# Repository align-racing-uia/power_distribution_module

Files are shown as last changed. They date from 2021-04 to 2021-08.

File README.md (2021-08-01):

<h1 align="center"> Power Distribution Module </h1> <br>
<p align="center">
    <a href="http://www.alignracing.no/">
      Align Racing UiA
    </a>
</p>

<!-- START doctoc generate TOC please keep comment here to allow auto update -->
<!-- DON'T EDIT THIS SECTION, INSTEAD RE-RUN doctoc TO UPDATE -->
## Table of contents

- [Introduction](#introduction)
- [Align Racing UiA](#alignracinguia)
- [Rules for file structure](#rulesforfilestructure)
- [License](#license)

<!-- END doctoc generated TOC please keep comment here to allow auto update -->

## Introduction

This is the repository for Align Racing's formula student race car's different systems.

## Align Racing UiA

<a href="http://www.alignracing.no/">Align Racing UiA (AR)</a> is a multidisciplinary student organisation at <a href="https://www.uia.no/">The University of Agder (UiA)</a>, that take part in the world’s largest yearly engineering competition; <a href="https://www.imeche.org/events/formula-student">Formula Student (FS)</a>. The organisation continuously consists of around 60 students, from a wide variety of disciplines. The competition includes developing, building, budgeting and marketing a small scale formula type racing car. AR takes this a bit further by having more focus on developing a strong organisation, open for all disciplines, that gives the members a taste of future work-life.

## Rules

## Contribution

## License
All content included in this Git repository is under the license:

Creative Commons Attribution-NonCommercial-ShareAlike 4.0 International

You are free to:
* <b> Share </b> — copy and redistribute the material in any medium or format
* <b> Adapt </b> — remix, transform, and build upon the material

Under the following terms:
* <b> Attribution </b> — You must give appropriate credit, provide a link to the license, and indicate if changes were made. You may do so in any reasonable manner, but not in any way that suggests the licensor endorses you or your use.
* <b> NonCommercial </b> — You may not use the material for commercial purposes.
* <b> ShareAlike </b> — If you remix, transform, or build upon the material, you must distribute your contributions under the same license as the original.
* <b> No additional restrictions </b> — You may not apply legal terms or technological measures that legally restrict others from doing anything the license permits.

<p align="center">
License
</p>

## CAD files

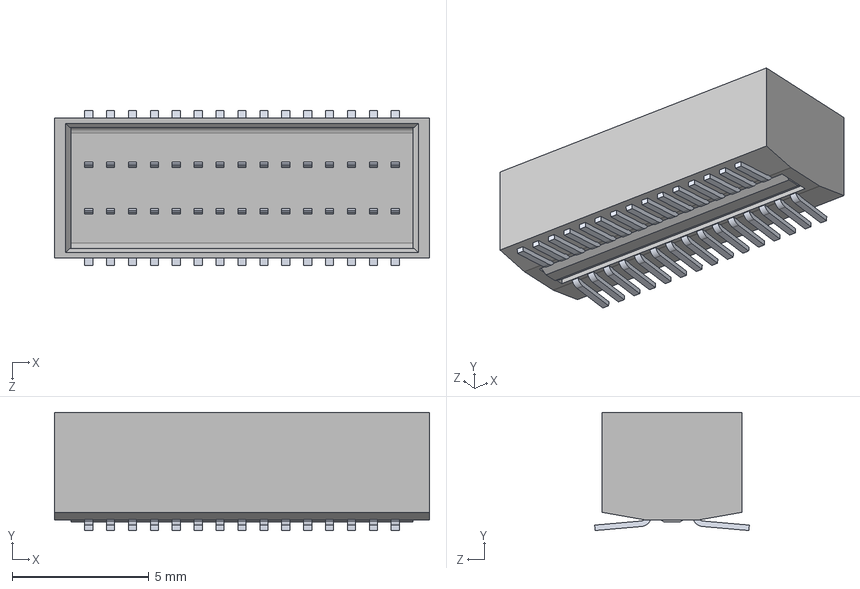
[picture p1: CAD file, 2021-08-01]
pdm_pcb/AR_PDM_v1/3d_objects/ACM-connector-pcb.step
13.7 x 4.31 x 5.65 mm

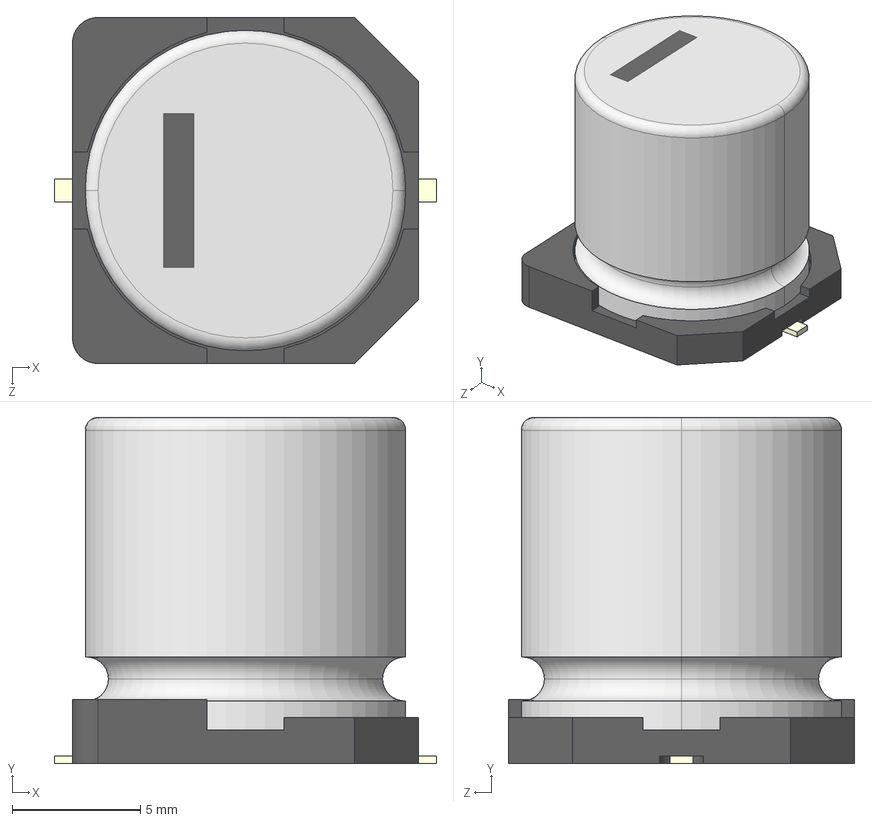
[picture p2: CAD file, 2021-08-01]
pdm_pcb/AR_PDM_v1_Simplified/3d_objects/H13.STEP
14.9 x 13.5 x 13.5 mm
標準SIZE CODE H13-001
標準SIZE CODE H13-002
標準SIZE CODE H13-003 x 2

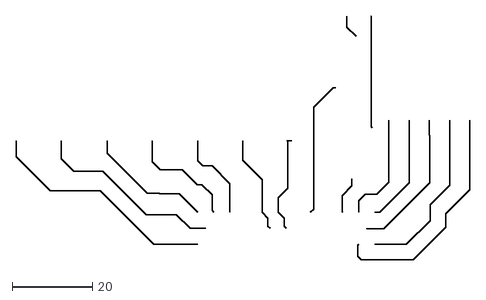
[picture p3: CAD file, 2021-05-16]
pdm_pcb/AR_PDM_v1_Simplified/test export/AR20_PDM_v1-F_Cu.dxf
112.8 x 60.5

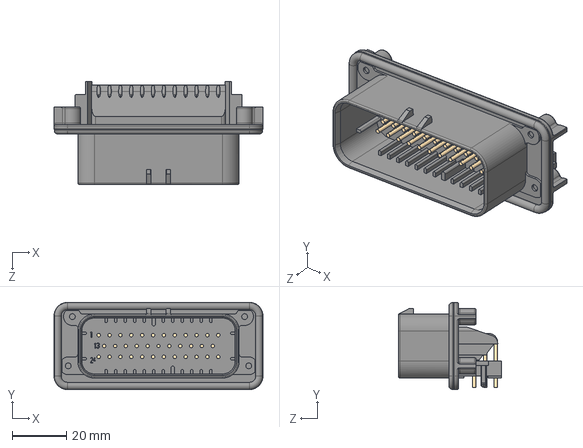
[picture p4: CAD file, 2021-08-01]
pdm_pcb/AR_PDM_v1/3d_objects/c-1-776163-1-s-3d.STEP
76.9 x 32.1 x 37.8 mm

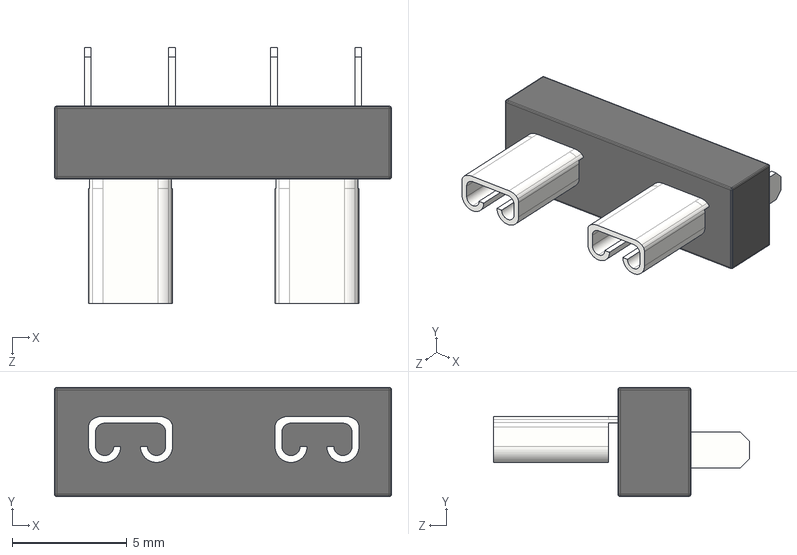
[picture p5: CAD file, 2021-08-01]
pdm_pcb/AR_PDM_v1_Simplified/3d_objects/Mini Blade Fuse Holder.STEP
14.7 x 4.75 x 11.1 mm
Body.step
Pins.step

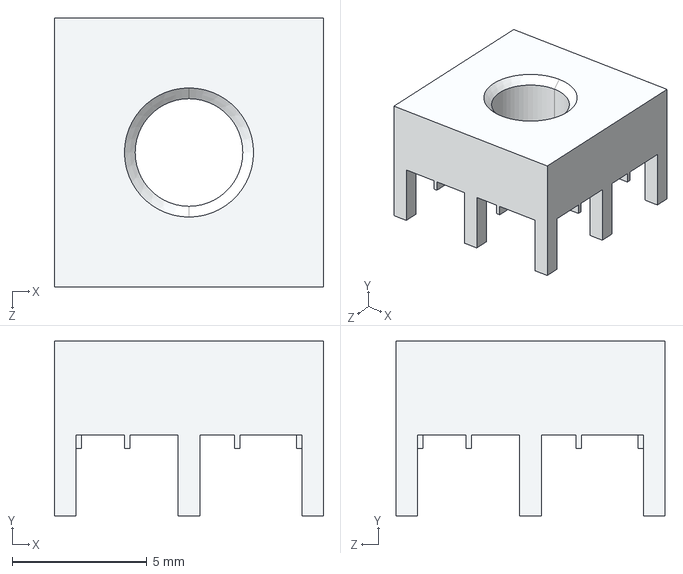
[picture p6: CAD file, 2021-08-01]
pdm_pcb/AR_PDM_v1/3d_objects/Wurth Studd m5.STEP
10.0 x 6.50 x 10.0 mm

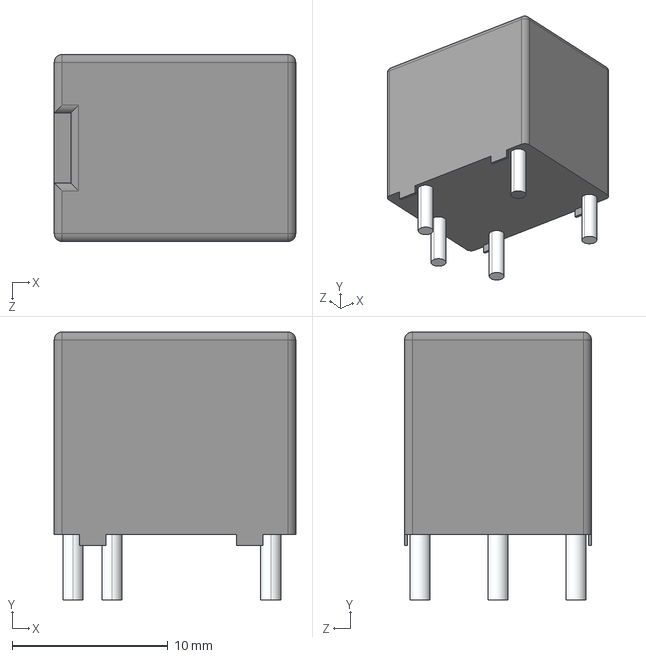
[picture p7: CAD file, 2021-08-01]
pdm_pcb/AR_PDM_v1/3d_objects/Relay.STEP
15.5 x 17.2 x 12.0 mm

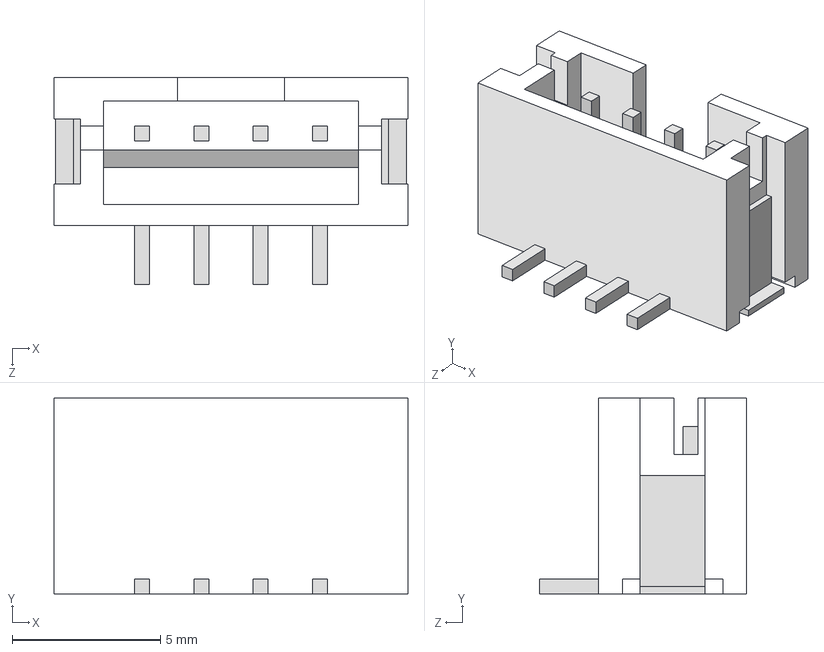
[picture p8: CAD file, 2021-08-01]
pdm_pcb/AR_PDM_v1_Simplified/3d_objects/B4B-PH-SM4-TB.STEP
12.0 x 6.60 x 7.00 mm

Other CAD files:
pdm_pcb/AR_PDM_v1_Simplified/3d_objects/Panasonic FK H13.STEP
pdm_pcb/AR_PDM_v1/3d_objects/Panasonic FK H13.STEP

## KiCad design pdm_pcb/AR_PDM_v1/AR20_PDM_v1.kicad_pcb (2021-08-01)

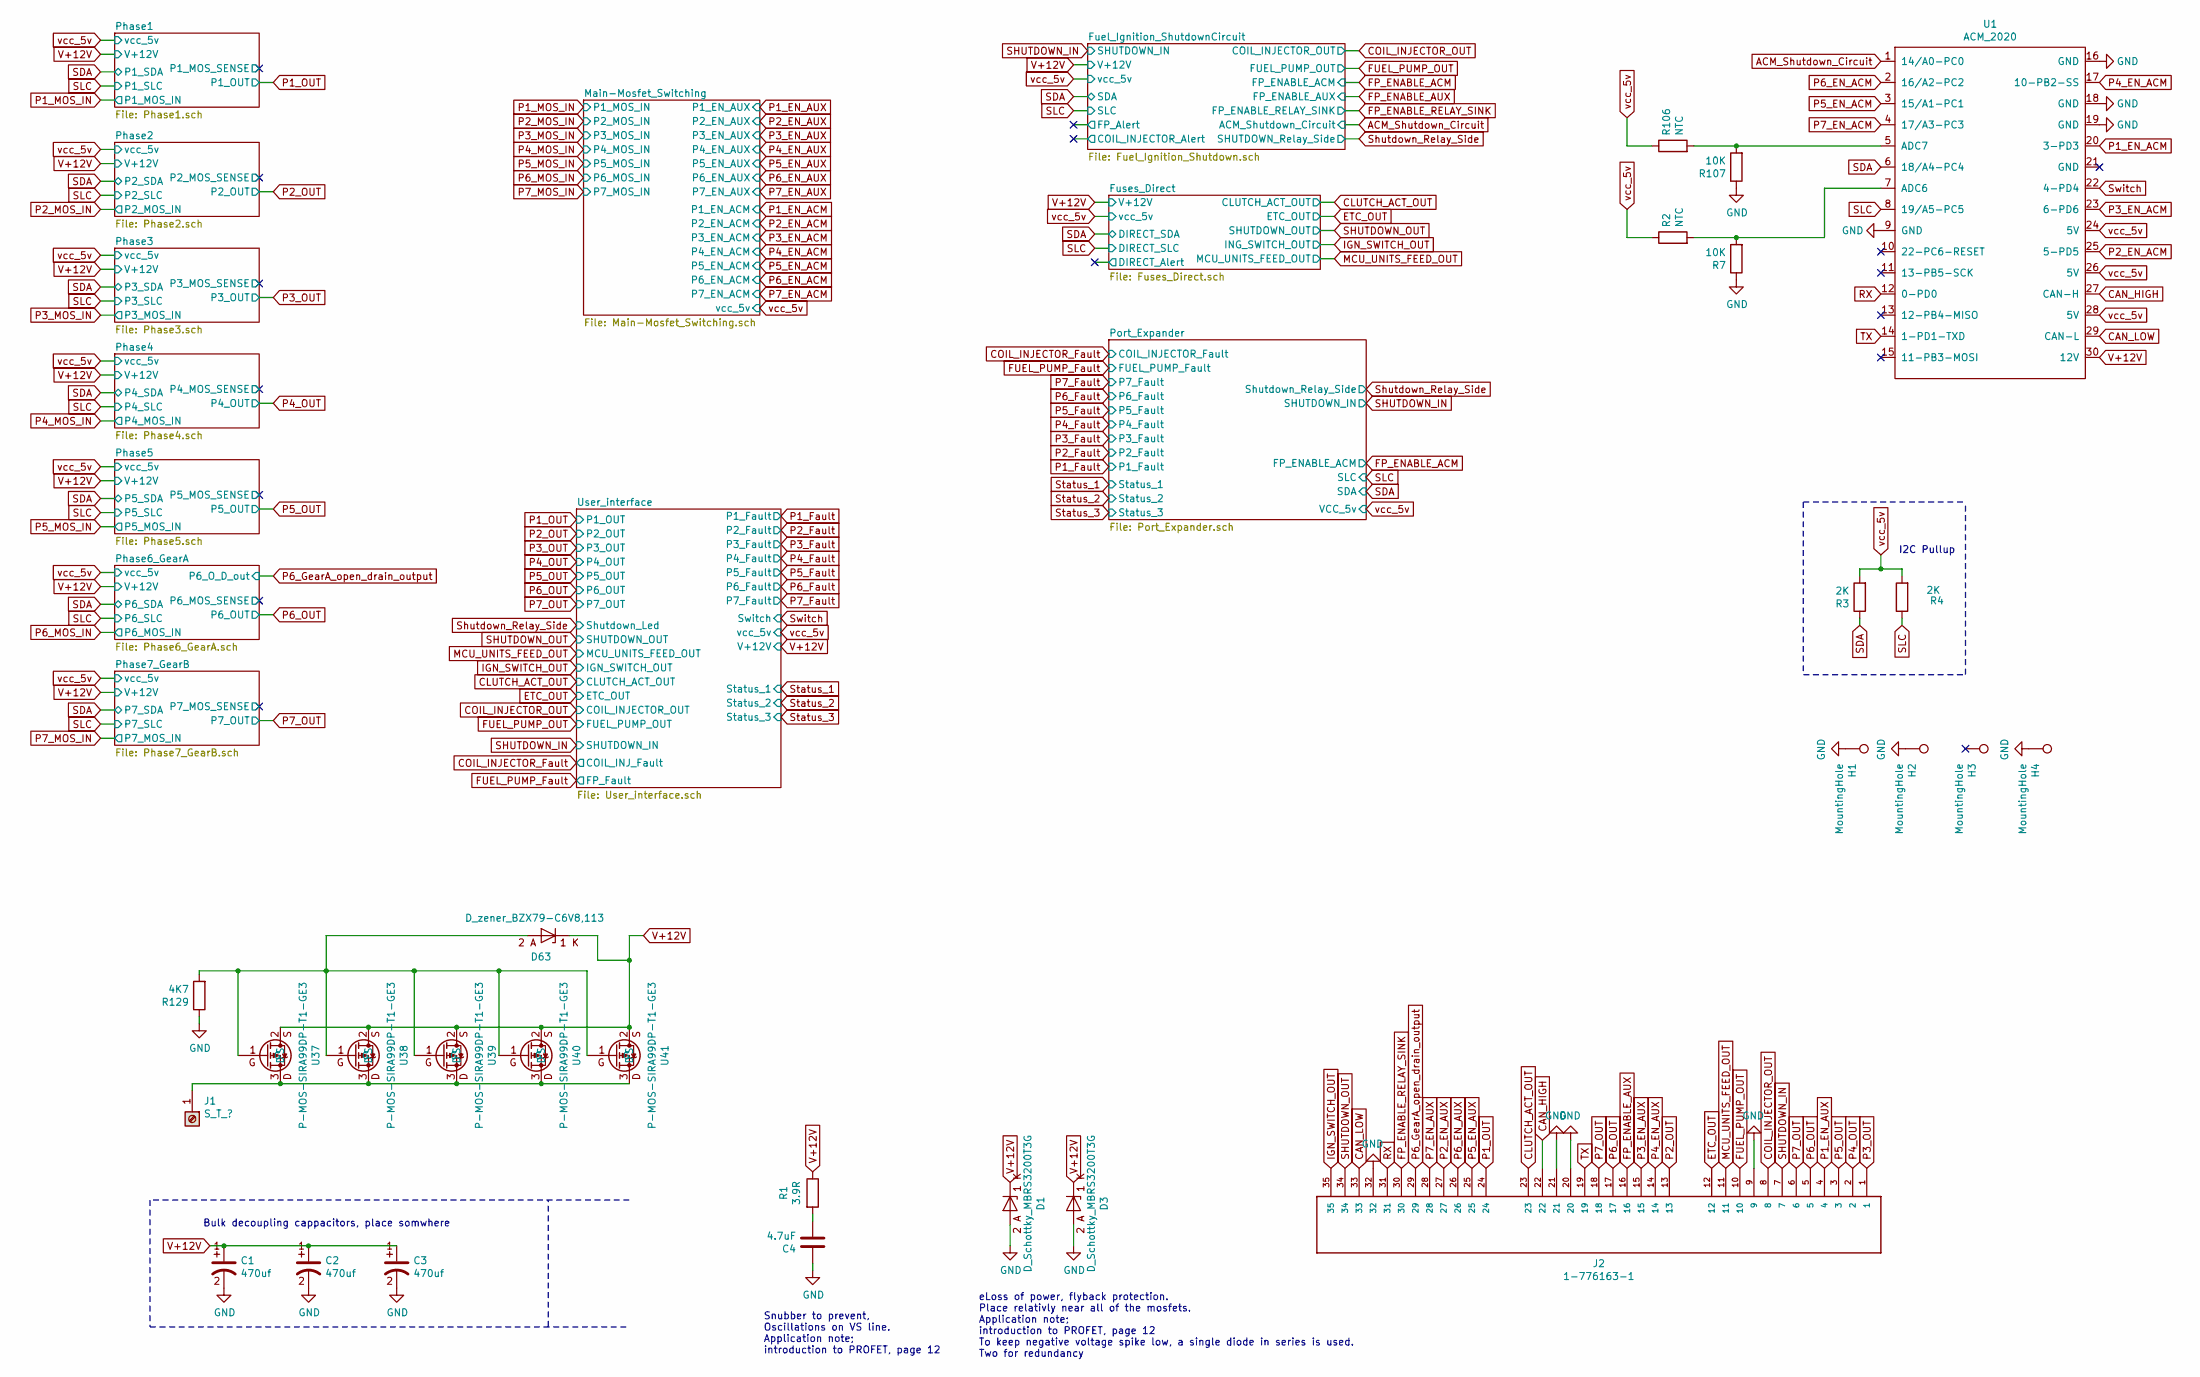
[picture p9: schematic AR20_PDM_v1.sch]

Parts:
C1, C2, C3: 470uf; CAPAE1350X1400N_EEV-FK1V471Q
C4: 4.7uF; C_1206_3216Metric
D1, D3: D_Schottky_MBRS3200T3G; D_SMB_Handsoldering
D63: D_zener_BZX79-C6V8,113; D_DO-35_BZX79-C6V8,113
H1, H2, H3, H4: MountingHole; MountingHole_3.2mm_M3_Pad_Via
J1: S_T_?; Wurth_74655095R_Screw_Post
J2: 1-776163-1; TE_1-776163-1
R1: 3.9R; R_2512_6332Metric
R2, R106: NTC; R_0603_1608Metric
R3, R4: 2K; R_0603_1608Metric
R7, R107: 10K; R_0603_1608Metric
R129: 4K7; R_0603_1608Metric
U1: ACM_2020; ACM_2020_Footprint_wo_silk
U37, U38, U39, U40, U41: P-MOS-SIRA99DP-T1-GE3

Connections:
ACM_Shutdown_Circuit: U1.1 (14/A0-PC0); also elsewhere on the board
CAN_HIGH: J2.22, U1.27 (CAN-H)
CAN_LOW: J2.33, U1.29 (CAN-L)
CLUTCH_ACT_OUT: J2.23; also elsewhere on the board
COIL_INJECTOR_OUT: J2.8; also elsewhere on the board
ETC_OUT: J2.12; also elsewhere on the board
FP_ENABLE_AUX: J2.16; also elsewhere on the board
FP_ENABLE_RELAY_SINK: J2.30; also elsewhere on the board
FUEL_PUMP_OUT: J2.10; also elsewhere on the board
IGN_SWITCH_OUT: J2.35; also elsewhere on the board
MCU_UNITS_FEED_OUT: J2.11; also elsewhere on the board
unnamed: C4.2, R1.2
unnamed: D63.2 (A), R129.2, U37.1 (G), U38.1 (G), U39.1 (G), U40.1 (G), U41.1 (G)
unnamed: J1.1, U37.3 (D), U38.3 (D), U39.3 (D), U40.3 (D), U41.3 (D)
unnamed: R2.2, R7.2, U1.7 (ADC6)
unnamed: R106.2, R107.2, U1.5 (ADC7)
P1_EN_ACM: U1.20 (3-PD3); also elsewhere on the board
P1_EN_AUX: J2.4; also elsewhere on the board
P1_OUT: J2.24; also elsewhere on the board
P2_EN_ACM: U1.25 (5-PD5); also elsewhere on the board
P2_EN_AUX: J2.27; also elsewhere on the board
P2_OUT: J2.13; also elsewhere on the board
P3_EN_ACM: U1.23 (6-PD6); also elsewhere on the board
P3_EN_AUX: J2.15; also elsewhere on the board
P3_OUT: J2.1; also elsewhere on the board
P4_EN_ACM: U1.17 (10-PB2-SS); also elsewhere on the board
P4_EN_AUX: J2.14; also elsewhere on the board
P4_OUT: J2.2; also elsewhere on the board
P5_EN_ACM: U1.3 (15/A1-PC1); also elsewhere on the board
P5_EN_AUX: J2.25; also elsewhere on the board
P5_OUT: J2.3; also elsewhere on the board
P6_EN_ACM: U1.2 (16/A2-PC2); also elsewhere on the board
P6_EN_AUX: J2.26; also elsewhere on the board
P6_GearA_open_drain_output: J2.29; also elsewhere on the board
P6_OUT: J2.5, J2.17; also elsewhere on the board
P7_EN_ACM: U1.4 (17/A3-PC3); also elsewhere on the board
P7_EN_AUX: J2.28; also elsewhere on the board
P7_OUT: J2.6, J2.18; also elsewhere on the board
RX: J2.31, U1.12 (0-PD0)
SDA: R3.1, U1.6 (18/A4-PC4); also elsewhere on the board
SHUTDOWN_IN: J2.7; also elsewhere on the board
SHUTDOWN_OUT: J2.34; also elsewhere on the board
SLC: R4.1, U1.8 (19/A5-PC5); also elsewhere on the board
Switch: U1.22 (4-PD4); also elsewhere on the board
TX: J2.19, U1.14 (1-PD1-TXD)
V+12V: C1.1, C2.1, C3.1, D1.1 (K), D3.1 (K), D63.1 (K), R1.1, U1.30 (12V), U37.2 (S), U38.2 (S), U39.2 (S), U40.2 (S), U41.2 (S); also elsewhere on the board
vcc_5v: R2.1, R3.2, R4.2, R106.1, U1.24 (5V), U1.26 (5V), U1.28 (5V); also elsewhere on the board

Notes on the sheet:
Bulk decoupling cappacitors, place somwhere
eLoss of power, flyback protection. Place relativly near all of the mosfets. Application note; introduction to PROFET, page 12 To keep negative voltage spike low, a single diode in series is used. Two for redundancy
I2C Pullup
Snubber to prevent, Oscillations on VS line. Application note; introduction to PROFET, page 12

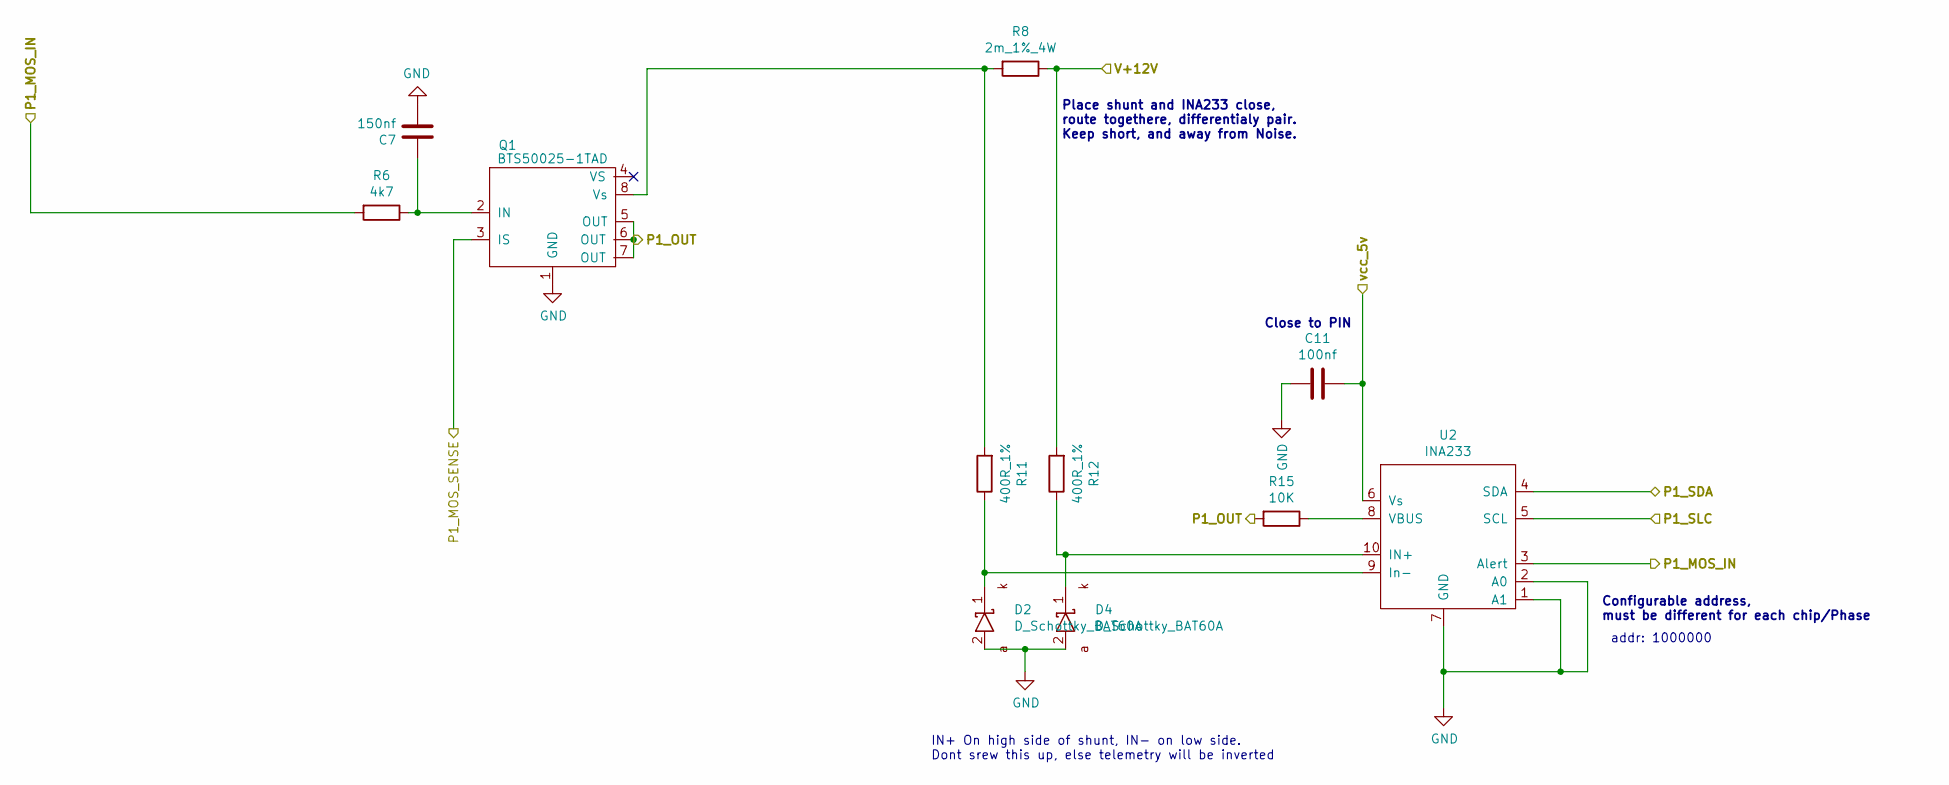
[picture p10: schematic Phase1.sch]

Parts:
C7: 150nf; C_0603_1608Metric
C11: 100nf; C_0603_1608Metric
D2, D4: D_Schottky_BAT60A; D_Shotky_BAT60_HandSoldering
Q1: BTS50025-1TAD; BTS500xx
R6: 4k7; R_0603_1608Metric
R8: 2m_1%_4W; R_2512_6332Metric
R11, R12: 400R_1%; R_0603_1608Metric
R15: 10K; R_0603_1608Metric
U2: INA233

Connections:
/Phase1/P1_MOS_SENSE: Q1.3 (IS)
unnamed: C7.1, Q1.2 (IN), R6.1
unnamed: D2.1 (K), R11.1, U2.9 (In-)
unnamed: D4.1 (K), R12.1, U2.10 (IN+)
unnamed: Q1.8 (Vs), R8.2, R11.2
unnamed: R15.1, U2.8 (VBUS)
P1_MOS_IN: R6.2, U2.3 (Alert); also elsewhere on the board
P1_OUT: Q1.5 (OUT), Q1.6 (OUT), Q1.7 (OUT), R15.2; also elsewhere on the board
SDA: U2.4 (SDA); also elsewhere on the board
SLC: U2.5 (SCL); also elsewhere on the board
V+12V: R8.1, R12.2; also elsewhere on the board
vcc_5v: C11.1, U2.6 (Vs); also elsewhere on the board

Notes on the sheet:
Close to PIN
Configurable address, must be different for each chip/Phase
addr: 1000000
Place shunt and INA233 close, route togethere, differentialy pair. Keep short, and away from Noise.
IN+ On high side of shunt, IN- on low side. Dont srew this up, else telemetry will be inverted

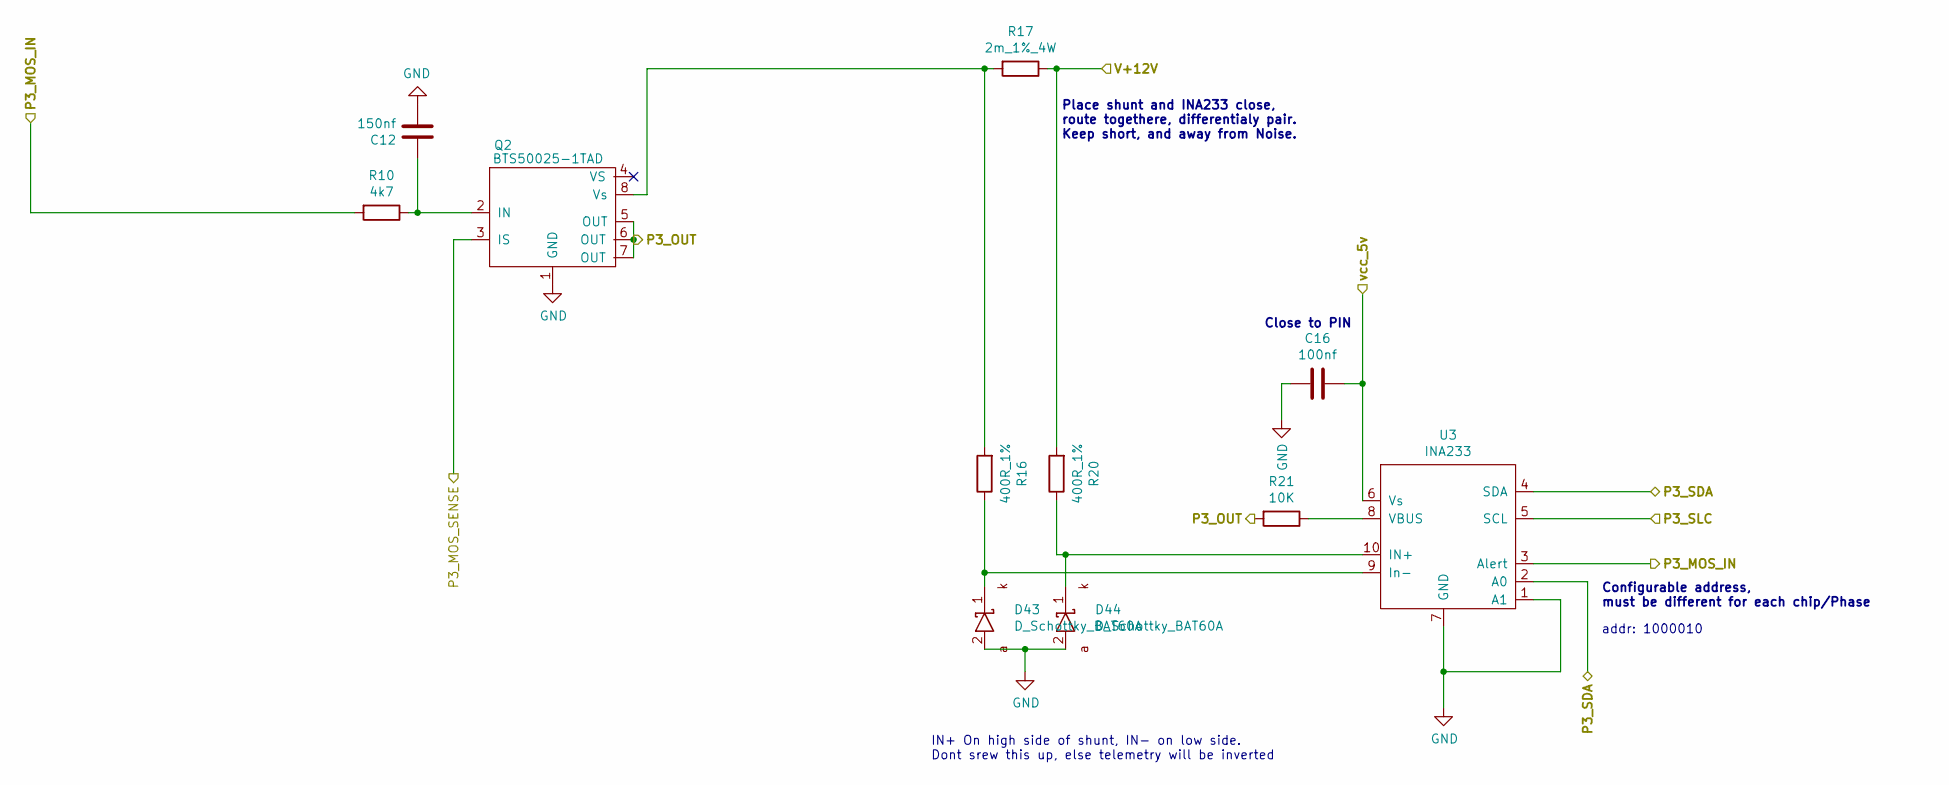
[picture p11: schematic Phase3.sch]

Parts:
C12: 150nf; C_0603_1608Metric
C16: 100nf; C_0603_1608Metric
D43, D44: D_Schottky_BAT60A; D_Shotky_BAT60_HandSoldering
Q2: BTS50025-1TAD; BTS500xx
R10: 4k7; R_0603_1608Metric
R16, R20: 400R_1%; R_0603_1608Metric
R17: 2m_1%_4W; R_2512_6332Metric
R21: 10K; R_0603_1608Metric
U3: INA233

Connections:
/Phase3/P3_MOS_SENSE: Q2.3 (IS)
unnamed: C12.1, Q2.2 (IN), R10.1
unnamed: D43.1 (K), R16.1, U3.9 (In-)
unnamed: D44.1 (K), R20.1, U3.10 (IN+)
unnamed: Q2.8 (Vs), R16.2, R17.2
unnamed: R21.1, U3.8 (VBUS)
P3_MOS_IN: R10.2, U3.3 (Alert); also elsewhere on the board
P3_OUT: Q2.5 (OUT), Q2.6 (OUT), Q2.7 (OUT), R21.2; also elsewhere on the board
SDA: U3.2 (A0), U3.4 (SDA); also elsewhere on the board
SLC: U3.5 (SCL); also elsewhere on the board
V+12V: R17.1, R20.2; also elsewhere on the board
vcc_5v: C16.1, U3.6 (Vs); also elsewhere on the board

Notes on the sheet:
Close to PIN
Configurable address, must be different for each chip/Phase
addr: 1000010
Place shunt and INA233 close, route togethere, differentialy pair. Keep short, and away from Noise.
IN+ On high side of shunt, IN- on low side. Dont srew this up, else telemetry will be inverted

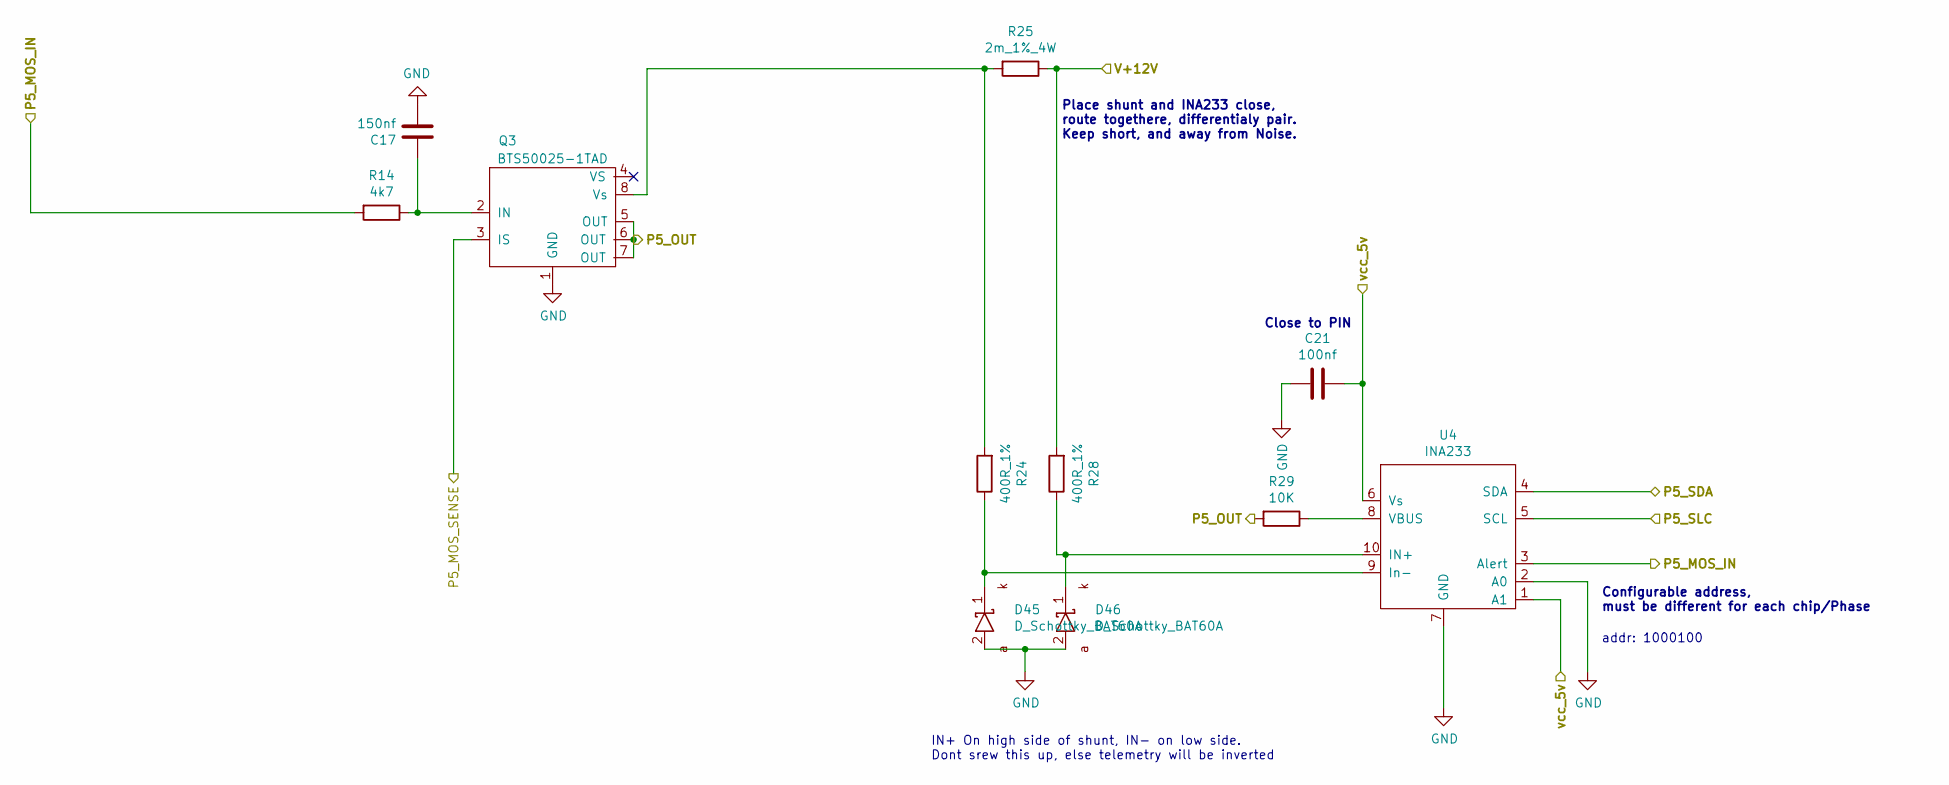
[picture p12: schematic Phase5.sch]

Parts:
C17: 150nf; C_0603_1608Metric
C21: 100nf; C_0603_1608Metric
D45, D46: D_Schottky_BAT60A; D_Shotky_BAT60_HandSoldering
Q3: BTS50025-1TAD; BTS500xx
R14: 4k7; R_0603_1608Metric
R24, R28: 400R_1%; R_0603_1608Metric
R25: 2m_1%_4W; R_2512_6332Metric
R29: 10K; R_0603_1608Metric
U4: INA233

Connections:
/Phase5/P5_MOS_SENSE: Q3.3 (IS)
unnamed: C17.1, Q3.2 (IN), R14.1
unnamed: D45.1 (K), R24.1, U4.9 (In-)
unnamed: D46.1 (K), R28.1, U4.10 (IN+)
unnamed: Q3.8 (Vs), R24.2, R25.2
unnamed: R29.1, U4.8 (VBUS)
P5_MOS_IN: R14.2, U4.3 (Alert); also elsewhere on the board
P5_OUT: Q3.5 (OUT), Q3.6 (OUT), Q3.7 (OUT), R29.2; also elsewhere on the board
SDA: U4.4 (SDA); also elsewhere on the board
SLC: U4.5 (SCL); also elsewhere on the board
V+12V: R25.1, R28.2; also elsewhere on the board
vcc_5v: C21.1, U4.1 (A1), U4.6 (Vs); also elsewhere on the board

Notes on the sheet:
Close to PIN
Configurable address, must be different for each chip/Phase
addr: 1000100
Place shunt and INA233 close, route togethere, differentialy pair. Keep short, and away from Noise.
IN+ On high side of shunt, IN- on low side. Dont srew this up, else telemetry will be inverted

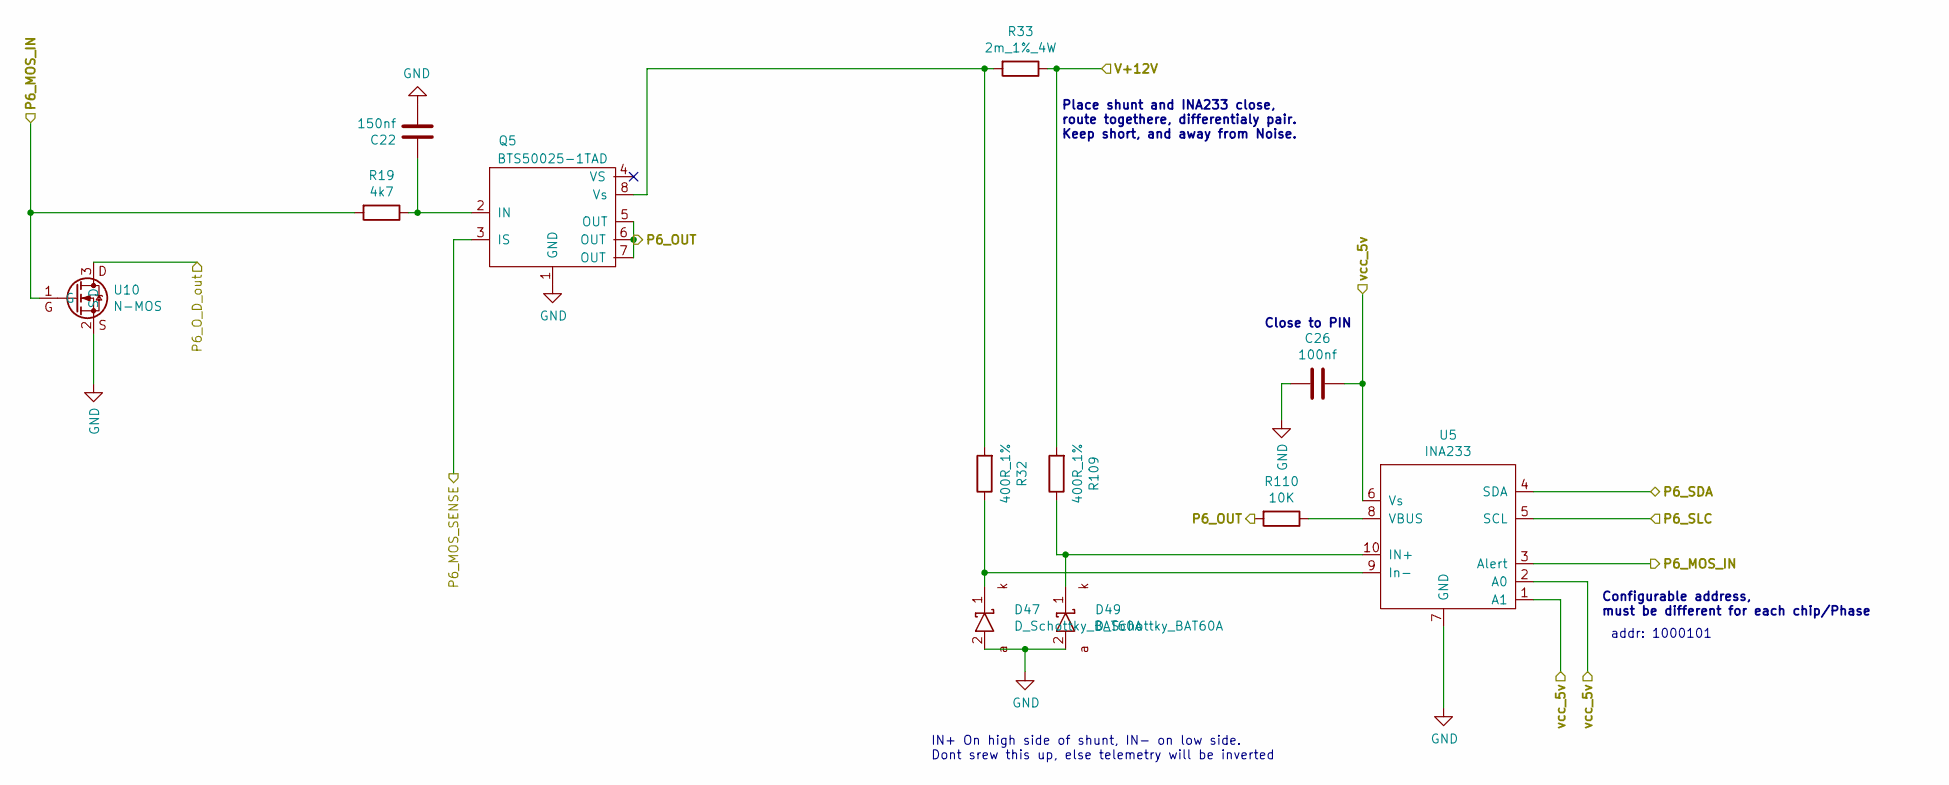
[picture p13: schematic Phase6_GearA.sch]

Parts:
C22: 150nf; C_0603_1608Metric
C26: 100nf; C_0603_1608Metric
D47, D49: D_Schottky_BAT60A; D_Shotky_BAT60_HandSoldering
Q5: BTS50025-1TAD; BTS500xx
R19: 4k7; R_0603_1608Metric
R32, R109: 400R_1%; R_0603_1608Metric
R33: 2m_1%_4W; R_2512_6332Metric
R110: 10K; R_0603_1608Metric
U5: INA233
U10: N-MOS; N-MOS-DMN6140L-13

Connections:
/Phase6_GearA/P6_MOS_SENSE: Q5.3 (IS)
unnamed: C22.1, Q5.2 (IN), R19.1
unnamed: D47.1 (K), R32.1, U5.9 (In-)
unnamed: D49.1 (K), R109.1, U5.10 (IN+)
unnamed: Q5.8 (Vs), R32.2, R33.2
unnamed: R110.1, U5.8 (VBUS)
P6_GearA_open_drain_output: U10.3 (D); also elsewhere on the board
P6_MOS_IN: R19.2, U5.3 (Alert), U10.1 (G); also elsewhere on the board
P6_OUT: Q5.5 (OUT), Q5.6 (OUT), Q5.7 (OUT), R110.2; also elsewhere on the board
SDA: U5.4 (SDA); also elsewhere on the board
SLC: U5.5 (SCL); also elsewhere on the board
V+12V: R33.1, R109.2; also elsewhere on the board
vcc_5v: C26.1, U5.1 (A1), U5.2 (A0), U5.6 (Vs); also elsewhere on the board

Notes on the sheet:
Close to PIN
Configurable address, must be different for each chip/Phase
addr: 1000101
Place shunt and INA233 close, route togethere, differentialy pair. Keep short, and away from Noise.
IN+ On high side of shunt, IN- on low side. Dont srew this up, else telemetry will be inverted

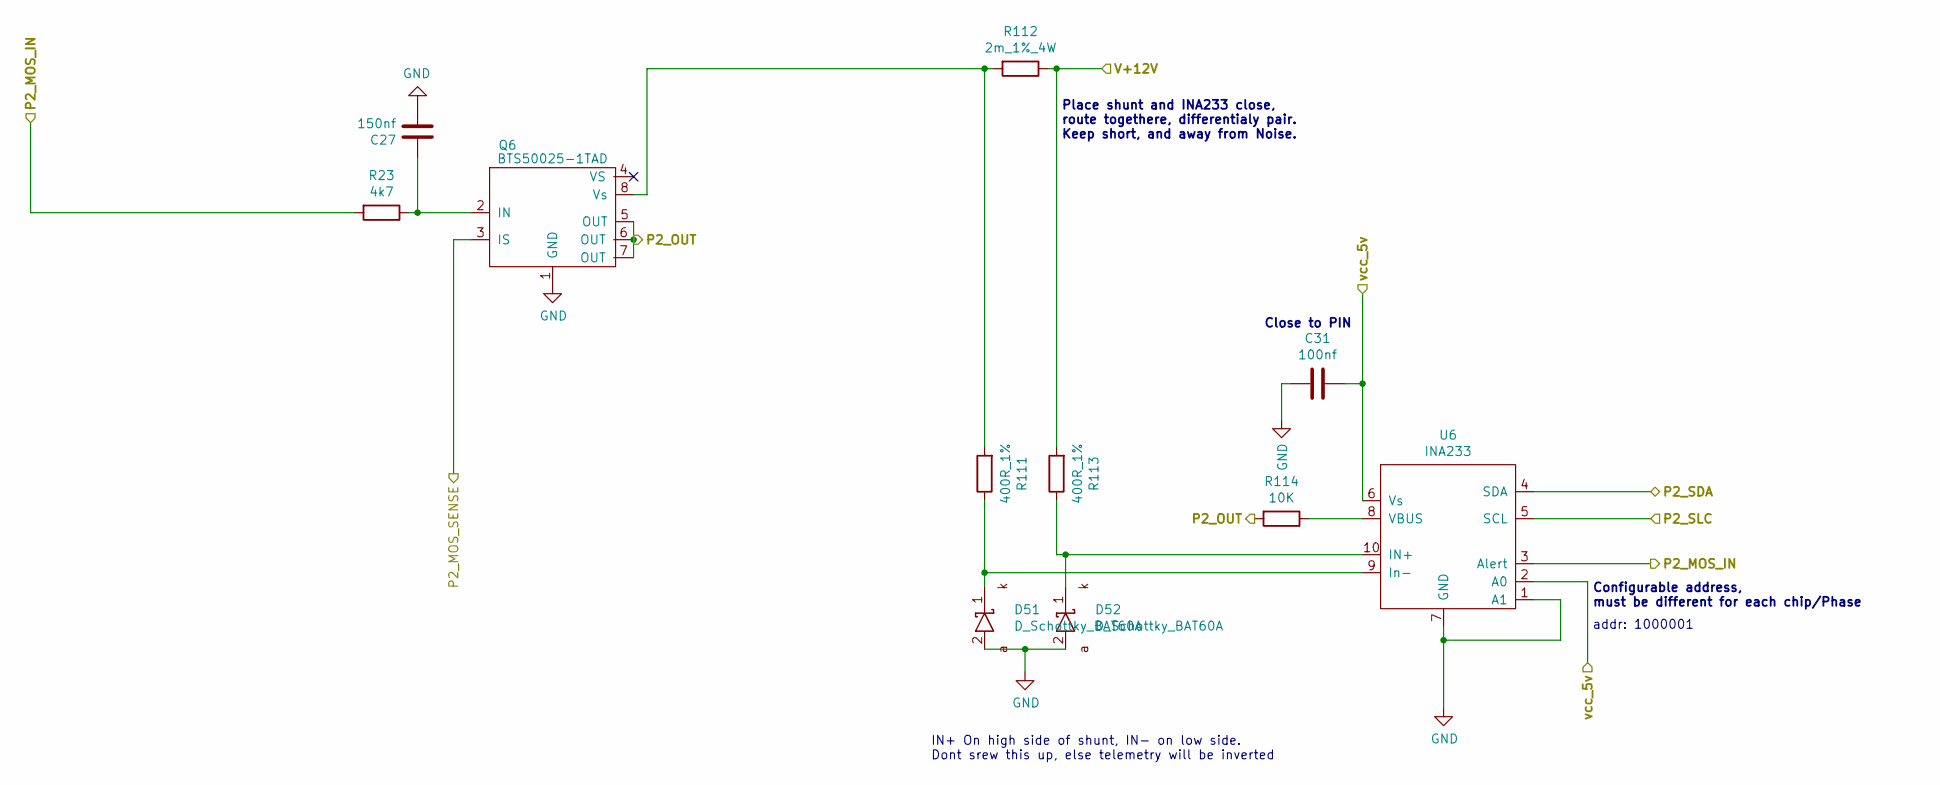
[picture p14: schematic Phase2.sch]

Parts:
C27: 150nf; C_0603_1608Metric
C31: 100nf; C_0603_1608Metric
D51, D52: D_Schottky_BAT60A; D_Shotky_BAT60_HandSoldering
Q6: BTS50025-1TAD; BTS500xx
R23: 4k7; R_0603_1608Metric
R111, R113: 400R_1%; R_0603_1608Metric
R112: 2m_1%_4W; R_2512_6332Metric
R114: 10K; R_0603_1608Metric
U6: INA233

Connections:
/Phase2/P2_MOS_SENSE: Q6.3 (IS)
unnamed: C27.1, Q6.2 (IN), R23.1
unnamed: D51.1 (K), R111.1, U6.9 (In-)
unnamed: D52.1 (K), R113.1, U6.10 (IN+)
unnamed: Q6.8 (Vs), R111.2, R112.2
unnamed: R114.1, U6.8 (VBUS)
P2_MOS_IN: R23.2, U6.3 (Alert); also elsewhere on the board
P2_OUT: Q6.5 (OUT), Q6.6 (OUT), Q6.7 (OUT), R114.2; also elsewhere on the board
SDA: U6.4 (SDA); also elsewhere on the board
SLC: U6.5 (SCL); also elsewhere on the board
V+12V: R112.1, R113.2; also elsewhere on the board
vcc_5v: C31.1, U6.2 (A0), U6.6 (Vs); also elsewhere on the board

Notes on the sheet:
Close to PIN
Configurable address, must be different for each chip/Phase
addr: 1000001
Place shunt and INA233 close, route togethere, differentialy pair. Keep short, and away from Noise.
IN+ On high side of shunt, IN- on low side. Dont srew this up, else telemetry will be inverted

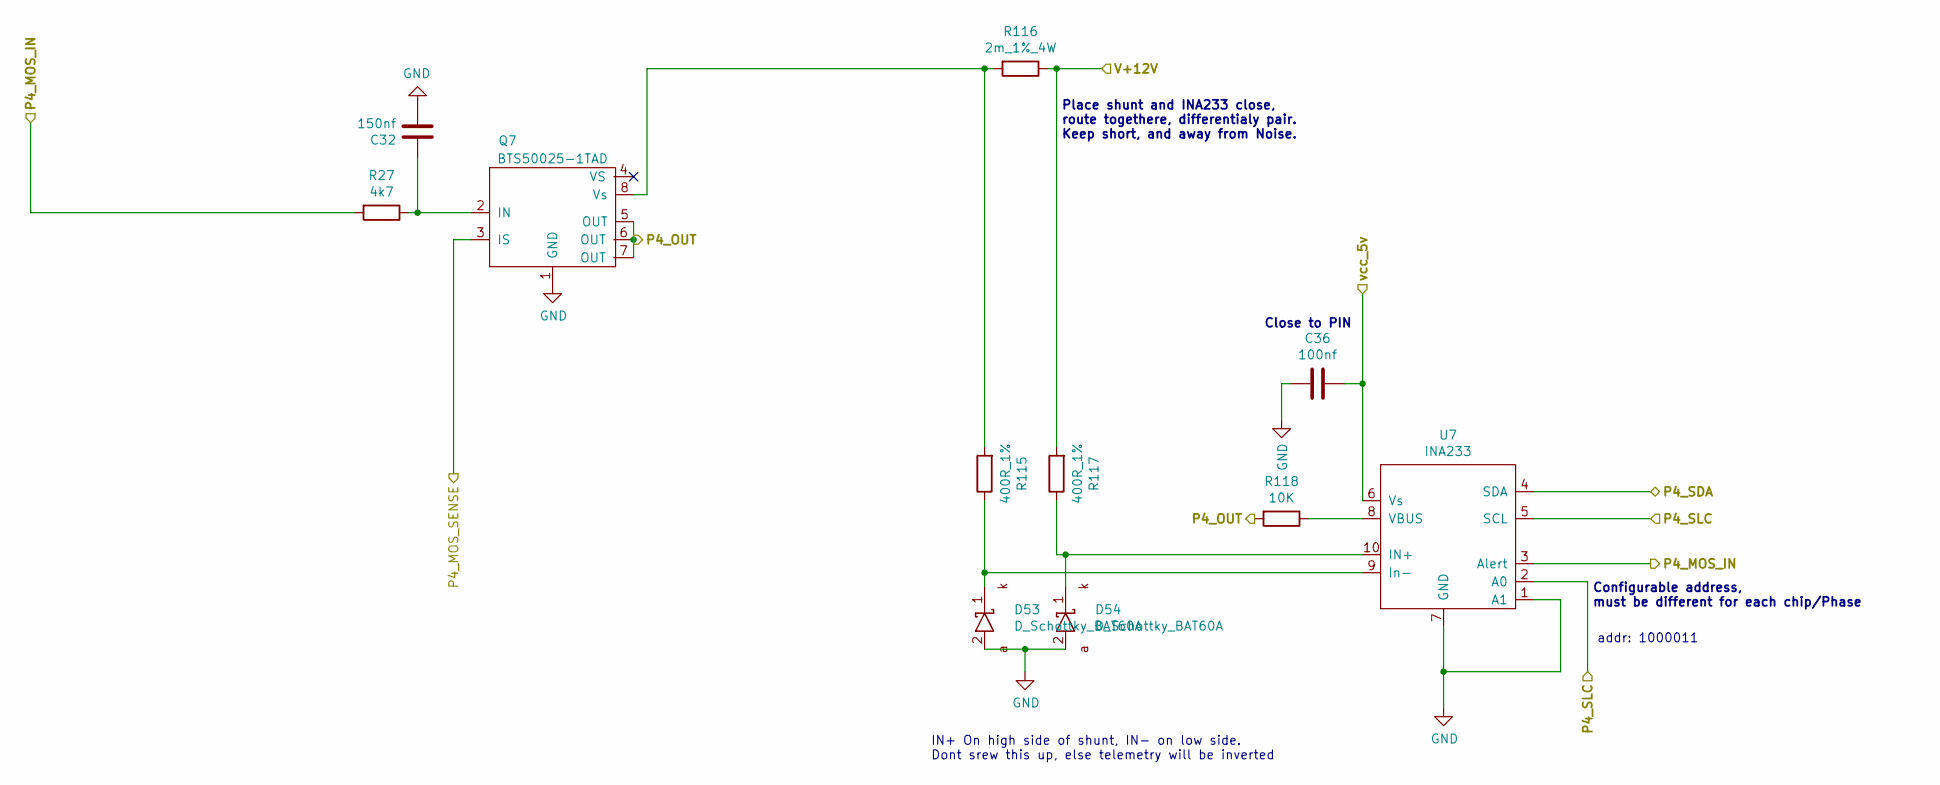
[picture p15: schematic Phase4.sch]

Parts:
C32: 150nf; C_0603_1608Metric
C36: 100nf; C_0603_1608Metric
D53, D54: D_Schottky_BAT60A; D_Shotky_BAT60_HandSoldering
Q7: BTS50025-1TAD; BTS500xx
R27: 4k7; R_0603_1608Metric
R115, R117: 400R_1%; R_0603_1608Metric
R116: 2m_1%_4W; R_2512_6332Metric
R118: 10K; R_0603_1608Metric
U7: INA233

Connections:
/Phase4/P4_MOS_SENSE: Q7.3 (IS)
unnamed: C32.1, Q7.2 (IN), R27.1
unnamed: D53.1 (K), R115.1, U7.9 (In-)
unnamed: D54.1 (K), R117.1, U7.10 (IN+)
unnamed: Q7.8 (Vs), R115.2, R116.2
unnamed: R118.1, U7.8 (VBUS)
P4_MOS_IN: R27.2, U7.3 (Alert); also elsewhere on the board
P4_OUT: Q7.5 (OUT), Q7.6 (OUT), Q7.7 (OUT), R118.2; also elsewhere on the board
SDA: U7.4 (SDA); also elsewhere on the board
SLC: U7.2 (A0), U7.5 (SCL); also elsewhere on the board
V+12V: R116.1, R117.2; also elsewhere on the board
vcc_5v: C36.1, U7.6 (Vs); also elsewhere on the board

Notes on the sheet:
Close to PIN
Configurable address, must be different for each chip/Phase
addr: 1000011
Place shunt and INA233 close, route togethere, differentialy pair. Keep short, and away from Noise.
IN+ On high side of shunt, IN- on low side. Dont srew this up, else telemetry will be inverted

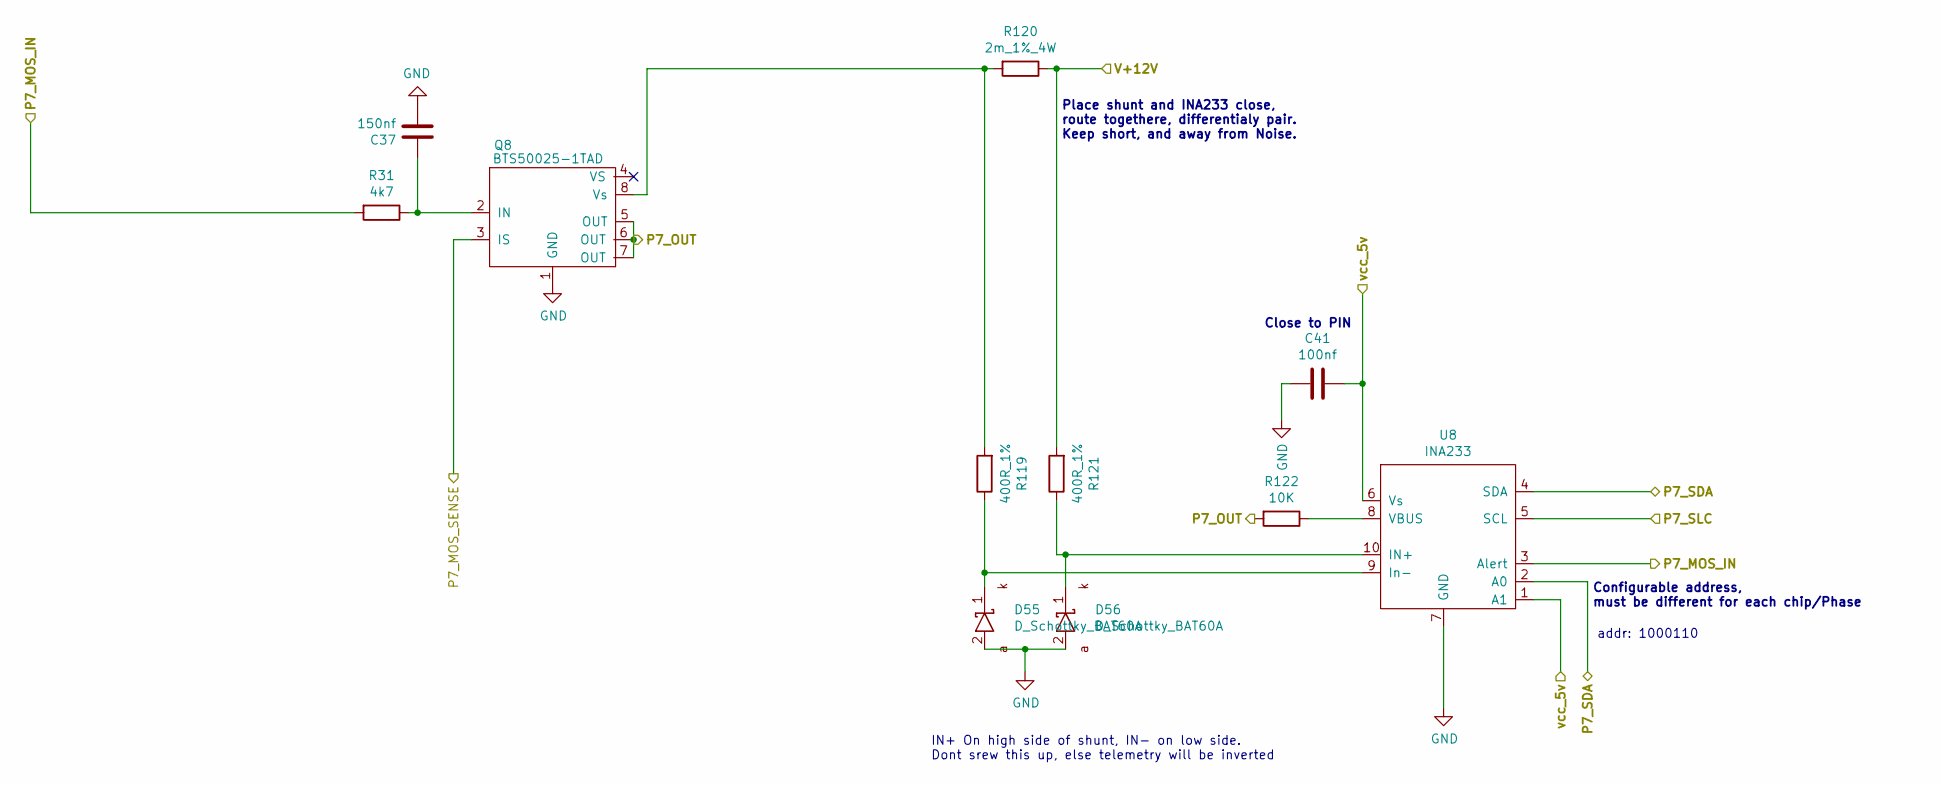
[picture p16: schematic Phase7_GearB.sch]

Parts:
C37: 150nf; C_0603_1608Metric
C41: 100nf; C_0603_1608Metric
D55, D56: D_Schottky_BAT60A; D_Shotky_BAT60_HandSoldering
Q8: BTS50025-1TAD; BTS500xx
R31: 4k7; R_0603_1608Metric
R119, R121: 400R_1%; R_0603_1608Metric
R120: 2m_1%_4W; R_2512_6332Metric
R122: 10K; R_0603_1608Metric
U8: INA233

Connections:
/Phase7_GearB/P7_MOS_SENSE: Q8.3 (IS)
unnamed: C37.1, Q8.2 (IN), R31.1
unnamed: D55.1 (K), R119.1, U8.9 (In-)
unnamed: D56.1 (K), R121.1, U8.10 (IN+)
unnamed: Q8.8 (Vs), R119.2, R120.2
unnamed: R122.1, U8.8 (VBUS)
P7_MOS_IN: R31.2, U8.3 (Alert); also elsewhere on the board
P7_OUT: Q8.5 (OUT), Q8.6 (OUT), Q8.7 (OUT), R122.2; also elsewhere on the board
SDA: U8.2 (A0), U8.4 (SDA); also elsewhere on the board
SLC: U8.5 (SCL); also elsewhere on the board
V+12V: R120.1, R121.2; also elsewhere on the board
vcc_5v: C41.1, U8.1 (A1), U8.6 (Vs); also elsewhere on the board

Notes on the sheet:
Close to PIN
Configurable address, must be different for each chip/Phase
addr: 1000110
Place shunt and INA233 close, route togethere, differentialy pair. Keep short, and away from Noise.
IN+ On high side of shunt, IN- on low side. Dont srew this up, else telemetry will be inverted

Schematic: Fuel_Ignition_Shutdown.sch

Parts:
C44, C45: 100nf; C_0603_1608Metric
D30, D31: D_Schottky_SS16M RS; Diode-SODFL2512X73N
D40: D_Zener_BZX585-C15,115; Diode-BZX585-C15,115
D48, D50: D_Schottky_MBRS3200T3G; D_SMB_Handsoldering
D57, D58, D59, D60: D_Schottky_BAT60A; D_Shotky_BAT60_HandSoldering
F6, F7: Fuse; FuseHolder
K1, K2: DIPxx-1Cxx-51x; Relay_wo_silkscreen
R5, R89, R92: 4K7; R_0603_1608Metric
R88, R91: 2m_1%_4W; R_2512_6332Metric
R105: 4k7; R_0603_1608Metric
R123, R124, R125, R126: 400R_1%; R_0603_1608Metric
U11, U13, U14: N-MOS; N-MOS-DMN6140L-13
U12: P-MOS; P-MOS-BSS83PH6327XTSA1
U29, U30: INA233

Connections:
/Fuel_Ignition_ShutdownCircuit/COIL_INJECTOR_Alert: U29.3 (Alert)
/Fuel_Ignition_ShutdownCircuit/FP_Alert: U30.3 (Alert)
ACM_Shutdown_Circuit: R89.2, U11.1 (G); also elsewhere on the board
COIL_INJECTOR_OUT: D48.1 (K), K1.7; also elsewhere on the board
FP_ENABLE_ACM: U13.1 (G); also elsewhere on the board
FP_ENABLE_AUX: R105.2; also elsewhere on the board
FP_ENABLE_RELAY_SINK: D31.2 (A), K2.2, U13.3 (D), U14.3 (D); also elsewhere on the board
FUEL_PUMP_OUT: D50.1 (K), K2.7; also elsewhere on the board
unnamed: D40.1 (K), R92.1, R105.1, U14.1 (G)
unnamed: D57.1 (K), R123.1, U29.10 (IN+)
unnamed: D58.1 (K), R124.2, U29.8 (VBUS), U29.9 (In-)
unnamed: D59.1 (K), R125.1, U30.10 (IN+)
unnamed: D60.1 (K), R126.2, U30.8 (VBUS), U30.9 (In-)
unnamed: F6.2, R91.1, R125.2
unnamed: F7.2, R88.1, R123.2
unnamed: K1.14, R88.2, R124.1
unnamed: K2.14, R91.2, R126.1
unnamed: R5.1, U11.3 (D), U12.1 (G)
SDA: U29.4 (SDA), U30.1 (A1), U30.4 (SDA); also elsewhere on the board
SHUTDOWN_IN: R5.2, U12.2 (S); also elsewhere on the board
SLC: U29.2 (A0), U29.5 (SCL), U30.5 (SCL); also elsewhere on the board
Shutdown_Relay_Side: D30.1 (K), D31.1 (K), K1.6, K2.6, U12.3 (D); also elsewhere on the board
V+12V: F6.1, F7.1; also elsewhere on the board
vcc_5v: C44.1, C45.1, U29.1 (A1), U29.6 (Vs), U30.6 (Vs); also elsewhere on the board

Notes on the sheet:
Close to PIN
Configurable address, must be different for each chip
Place shunt and INA233 close
addr: 1000111
addr: 1001000
Use Logic Level Mosfets. (Gs Threshold <3.3V)

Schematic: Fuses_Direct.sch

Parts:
C46: 100nf; C_0603_1608Metric
D61, D62: D_Schottky_BAT60A; D_Shotky_BAT60_HandSoldering
F1, F2, F3, F4, F5: Fuse; FuseHolder
R93, R94: 2m_1%_4W; R_2512_6332Metric
R127, R128: 400R_1%; R_0603_1608Metric
U31: INA233

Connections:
/Fuses_Direct/DIRECT_Alert: U31.3 (Alert)
CLUTCH_ACT_OUT: F3.1; also elsewhere on the board
ETC_OUT: F5.1; also elsewhere on the board
IGN_SWITCH_OUT: F1.1; also elsewhere on the board
MCU_UNITS_FEED_OUT: F2.1; also elsewhere on the board
unnamed: D61.1 (K), R127.1, U31.10 (IN+)
unnamed: D62.1 (K), R128.1, U31.8 (VBUS), U31.9 (In-)
unnamed: F1.2, F2.2, F3.2, F4.2, F5.2, R93.1, R94.1, R128.2
SDA: U31.1 (A1), U31.4 (SDA); also elsewhere on the board
SHUTDOWN_OUT: F4.1; also elsewhere on the board
SLC: U31.5 (SCL); also elsewhere on the board
V+12V: R93.2, R94.2, R127.2; also elsewhere on the board
vcc_5v: C46.1, U31.2 (A0), U31.6 (Vs); also elsewhere on the board

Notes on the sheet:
Configurable address, must be different for each chip
Close to PIN
Place shunt close to INA233
addr: 1001001
IN+ On high side of shunt, IN- on low side. Dont srew this up, else telemetry will be inverted
Place shunt and INA233 close, route togethere, differentialy pair. Keep short, and away from Noise.

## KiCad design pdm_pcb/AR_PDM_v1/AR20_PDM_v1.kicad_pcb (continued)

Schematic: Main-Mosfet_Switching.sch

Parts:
D26, D27, D28, D29, D32, D33, D34: D_Zener_BZX585-C15,115; Diode-BZX585-C15,115
R9, R13, R18, R22, R26, R30, R34, R35, R36, R37, R38, R39, R42, R43, R48, R49, R56, R57, R62, R63, R65, R66, R69, R70, R72, R73, R78, R79, R80, R81, R83, R85, R86, R87, R95: 4k7; R_0603_1608Metric
SW1: SW_DIP_x07; Dip-Switch-14
U15, U16, U17, U18, U19, U20, U21, U22, U23, U24, U25, U26, U27, U28: N-MOS; N-MOS-DMN6140L-13

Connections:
unnamed: D26.1 (K), R9.1, R35.1, U15.1 (G)
unnamed: D27.1 (K), R13.1, R36.1, U16.1 (G)
unnamed: D28.1 (K), R18.1, R37.1, U17.1 (G)
unnamed: D29.1 (K), R22.1, R38.1, U18.1 (G)
unnamed: D32.1 (K), R26.1, R39.1, U19.1 (G)
unnamed: D33.1 (K), R30.1, R42.1, U20.1 (G)
unnamed: D34.1 (K), R34.1, R43.1, U21.1 (G)
unnamed: R48.1, U15.3 (D), U22.1 (G)
unnamed: R49.1, U16.3 (D), U23.1 (G)
unnamed: R56.1, U17.3 (D), U24.1 (G)
unnamed: R57.1, U18.3 (D), U25.1 (G)
unnamed: R62.1, U19.3 (D), U26.1 (G)
unnamed: R63.1, U20.3 (D), U27.1 (G)
unnamed: R65.1, U21.3 (D), U28.1 (G)
unnamed: SW1.1, U22.3 (D)
unnamed: SW1.2, U23.3 (D)
unnamed: SW1.3, U24.3 (D)
unnamed: SW1.4, U25.3 (D)
unnamed: SW1.5, U26.3 (D)
unnamed: SW1.6, U27.3 (D)
unnamed: SW1.7, U28.3 (D)
P1_EN_ACM: R66.1, R69.1; also elsewhere on the board
P1_EN_AUX: R9.2; also elsewhere on the board
P1_MOS_IN: R69.2, SW1.14; also elsewhere on the board
P2_EN_ACM: R70.1, R72.1; also elsewhere on the board
P2_EN_AUX: R13.2; also elsewhere on the board
P2_MOS_IN: R72.2, SW1.13; also elsewhere on the board
P3_EN_ACM: R73.1, R78.1; also elsewhere on the board
P3_EN_AUX: R18.2; also elsewhere on the board
P3_MOS_IN: R78.2, SW1.12; also elsewhere on the board
P4_EN_ACM: R79.1, R80.1; also elsewhere on the board
P4_EN_AUX: R22.2; also elsewhere on the board
P4_MOS_IN: R80.2, SW1.11; also elsewhere on the board
P5_EN_ACM: R81.1, R83.1; also elsewhere on the board
P5_EN_AUX: R26.2; also elsewhere on the board
P5_MOS_IN: R83.2, SW1.10; also elsewhere on the board
P6_EN_ACM: R85.1, R86.1; also elsewhere on the board
P6_EN_AUX: R30.2; also elsewhere on the board
P6_MOS_IN: R86.2, SW1.9; also elsewhere on the board
P7_EN_ACM: R87.1, R95.1; also elsewhere on the board
P7_EN_AUX: R34.2; also elsewhere on the board
P7_MOS_IN: R95.2, SW1.8; also elsewhere on the board
vcc_5v: R48.2, R49.2, R56.2, R57.2, R62.2, R63.2, R65.2; also elsewhere on the board

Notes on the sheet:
Use Logic Level Mosfets. In order for a low voltage signal to be able to controll AUX inputs. for exsample an AXU microcprosessor, or other controll logic. (Gs Threshold <3.3V or <5V might be used) mos array altso might be used
Protected AUX Input stages, Firs Nmos is resistive inverter, for the input. and second Nmos to controll the "in" signal of the power mosfet (big thingy) Dip switch is to disable AUX inputs. AUX will override the Microprosessor in off state. That mean AUX inputs has to be disable by the dip switch, 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
Side note: Its possible to remove the dip switch, at the cost of extra microprosessor, outputs. Possibly altso more overall traces. However due to its simplicity and rubustness, the dip switch stays, for now.

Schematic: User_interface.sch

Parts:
D5: Led_Red_P1_Fault; LED_1206_3216Metric
D6: Led_Green_P1_Active; LED_1206_3216Metric
D7: Led_Red_P2_Fault; LED_1206_3216Metric
D8: Led_Green_P2_Active; LED_1206_3216Metric
D9: Led_Red_P3_Fault; LED_1206_3216Metric
D10: Led_Green_P3_Active; LED_1206_3216Metric
D11: Led_Red_P4_Fault; LED_1206_3216Metric
D12: Led_Green_P4_Active; LED_1206_3216Metric
D13: Led_Red_P5_Fault; LED_1206_3216Metric
D14: Led_Green_P5_Active; LED_1206_3216Metric
D15: Led_Red_P6_Fault; LED_1206_3216Metric
D16: Led_Green_P6_Active; LED_1206_3216Metric
D17: Led_Red_P7_Fault; LED_1206_3216Metric
D18: Led_Green_P7_Active; LED_1206_3216Metric
D19: Led_Green_FP_Active; LED_1206_3216Metric
D20: Led_Green_COIL_INJ_Active; LED_1206_3216Metric
D21: Led_Green_Shutdown_Circuit_Supply; LED_1206_3216Metric
D22: Led_Green_Shutdown_IN_Active; LED_1206_3216Metric
D23: Led_Red_COIL_INJ_Fault; LED_1206_3216Metric
D24: Led_Red_FP_Fault; LED_1206_3216Metric
D25: Led_Red_CLUTCH_ACT_Fault; LED_1206_3216Metric
D35: Led_Red_MCU_Feed_Fault; LED_1206_3216Metric
D36: Led_Red_ETC_OUT_Fault; LED_1206_3216Metric
D37: Led_Red_Shutdown_out_Fault; LED_1206_3216Metric
D38: Led_Red_ING_Switch_Fault; LED_1206_3216Metric
D39: Led_Green_Status1; LED_1206_3216Metric
D41: Led_Green_Status2; LED_1206_3216Metric
D42: Led_Green_Status3; LED_1206_3216Metric
JP1: WireJumper; WireJumper_15mm
JP2: WireJumper; WireJumper_25mm
JP3: WireJumper; WireJumper_20mm
JP4: WireJumper; WireJumper_10.5mm
P1: B4B-PH-SM4-TB; JST_B4B-PH-SM4-TB
R44, R46, R50, R52, R54, R58, R60, R74, R75, R82, R90, R104, R108: 500R; R_0603_1608Metric
R45, R47, R51, R53, R55, R59, R61, R64, R67, R68, R71, R77, R97, R99, R101, R103: 2K; R_0603_1608Metric
R76, R84, R96, R98, R100, R102: 4k7; R_0603_1608Metric
U32, U33, U34, U35, U36: P-MOS; P-MOS-BSS83PH6327XTSA1

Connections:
CLUTCH_ACT_OUT: JP1.1; also elsewhere on the board
COIL_INJECTOR_Fault: R74.2; also elsewhere on the board
COIL_INJECTOR_OUT: D20.2 (A); also elsewhere on the board
ETC_OUT: JP3.1; also elsewhere on the board
FUEL_PUMP_Fault: R75.2; also elsewhere on the board
FUEL_PUMP_OUT: D19.2 (A); also elsewhere on the board
IGN_SWITCH_OUT: JP4.1; also elsewhere on the board
MCU_UNITS_FEED_OUT: JP2.1; also elsewhere on the board
unnamed: D5.1 (K), R44.1
unnamed: D6.1 (K), R45.1
unnamed: D7.1 (K), R46.1
unnamed: D8.1 (K), R47.1
unnamed: D9.1 (K), R50.1
unnamed: D10.1 (K), R51.1
unnamed: D11.1 (K), R52.1
unnamed: D12.1 (K), R53.1
unnamed: D13.1 (K), R54.1
unnamed: D14.1 (K), R55.1
unnamed: D15.1 (K), R58.1
unnamed: D16.1 (K), R59.1
unnamed: D17.1 (K), R60.1
unnamed: D18.1 (K), R61.1
unnamed: D19.1 (K), R64.1
unnamed: D20.1 (K), R67.1
unnamed: D21.1 (K), R68.1
unnamed: D22.1 (K), R71.1
unnamed: D23.1 (K), R74.1
unnamed: D24.1 (K), R75.1
unnamed: D25.2 (A), R77.2
unnamed: D35.2 (A), R97.2
unnamed: D36.2 (A), R99.2
unnamed: D37.2 (A), R101.2
unnamed: D38.2 (A), R103.2
unnamed: D39.1 (K), R90.1
unnamed: D41.1 (K), R104.1
unnamed: D42.1 (K), R108.1
unnamed: JP1.2, R76.1, U32.1 (G)
unnamed: JP2.2, R96.1, U33.1 (G)
unnamed: JP3.2, R98.1, U34.1 (G)
unnamed: JP4.2, R102.1, U36.1 (G)
unnamed: P1.3, R82.1
unnamed: R77.1, U32.3 (D)
unnamed: R97.1, U33.3 (D)
unnamed: R99.1, U34.3 (D)
unnamed: R101.1, U35.3 (D)
unnamed: R103.1, U36.3 (D)
P1_Fault: R44.2; also elsewhere on the board
P1_OUT: D6.2 (A); also elsewhere on the board
P2_Fault: R46.2; also elsewhere on the board
P2_OUT: D8.2 (A); also elsewhere on the board
P3_Fault: R50.2; also elsewhere on the board
P3_OUT: D10.2 (A); also elsewhere on the board
P4_Fault: R52.2; also elsewhere on the board
P4_OUT: D12.2 (A); also elsewhere on the board
P5_Fault: R54.2; also elsewhere on the board
P5_OUT: D14.2 (A); also elsewhere on the board
P6_Fault: R58.2; also elsewhere on the board
P6_OUT: D16.2 (A); also elsewhere on the board
P7_Fault: R60.2; also elsewhere on the board
P7_OUT: D18.2 (A); also elsewhere on the board
SHUTDOWN_IN: D22.2 (A); also elsewhere on the board
SHUTDOWN_OUT: R100.1, U35.1 (G); also elsewhere on the board
Shutdown_Relay_Side: D21.2 (A); also elsewhere on the board
Status_1: R90.2; also elsewhere on the board
Status_2: R104.2; also elsewhere on the board
Status_3: R108.2; also elsewhere on the board
Switch: P1.2, R84.1; also elsewhere on the board
V+12V: U32.2 (S), U33.2 (S), U34.2 (S), U35.2 (S), U36.2 (S); also elsewhere on the board
vcc_5v: D5.2 (A), D7.2 (A), D9.2 (A), D11.2 (A), D13.2 (A), D15.2 (A), D17.2 (A), D23.2 (A), D24.2 (A), D39.2 (A), D41.2 (A), D42.2 (A), P1.1, R82.2; also elsewhere on the board

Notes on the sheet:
Status and fault LED for digital fused phases. GREEN FOR STATUS, RED FOR FAULT
Leds sink to MCU/port expander.
Red led lights up, upon burnt fuse.
Activity LED for mechanical/relay power. GREEN LEDS
Failt LED for mechanical/relay power. RED LEDS

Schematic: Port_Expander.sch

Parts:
C42, C43: 100nf; C_0603_1608Metric
R40, R41, R130, R131, R132, R133, R134, R135, R136, R137: 4K7; R_0603_1608Metric
U9: TCA6424ARGJR; QFN50P500X500X60-33N
U42, U43: N-MOS; N-MOS-DMN6140L-13

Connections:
COIL_INJECTOR_Fault: U9.11 (P12); also elsewhere on the board
FP_ENABLE_ACM: U9.20 (P23); also elsewhere on the board
FUEL_PUMP_Fault: U9.12 (P13); also elsewhere on the board
unnamed: R40.1, U9.28 (~RESET~)
unnamed: R41.2, U9.32 (~INT~)
unnamed: R130.1, R136.2, U42.3 (D)
unnamed: R131.1, R137.2, U43.3 (D)
unnamed: R133.2, U42.1 (G)
unnamed: R135.2, U43.1 (G)
unnamed: R136.1, U9.14 (P15)
unnamed: R137.1, U9.13 (P14)
P1_Fault: U9.7 (P06); also elsewhere on the board
P2_Fault: U9.6 (P05); also elsewhere on the board
P3_Fault: U9.5 (P04); also elsewhere on the board
P4_Fault: U9.4 (P03); also elsewhere on the board
P5_Fault: U9.3 (P02); also elsewhere on the board
P6_Fault: U9.2 (P01); also elsewhere on the board
P7_Fault: U9.1 (P00); also elsewhere on the board
SDA: U9.30 (SDA); also elsewhere on the board
SHUTDOWN_IN: R134.2, R135.1; also elsewhere on the board
SLC: U9.29 (SCL); also elsewhere on the board
Shutdown_Relay_Side: R132.2, R133.1; also elsewhere on the board
Status_1: U9.10 (P11); also elsewhere on the board
Status_2: U9.9 (P10); also elsewhere on the board
Status_3: U9.8 (P07); also elsewhere on the board
vcc_5v: C42.1, C43.1, R40.2, R41.1, R130.2, R131.2, U9.27 (VCCP), U9.31 (VCCI); also elsewhere on the board

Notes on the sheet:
ADDR to gnd, i2c Address: 0100010
Shutdown circuit feedback Inverted

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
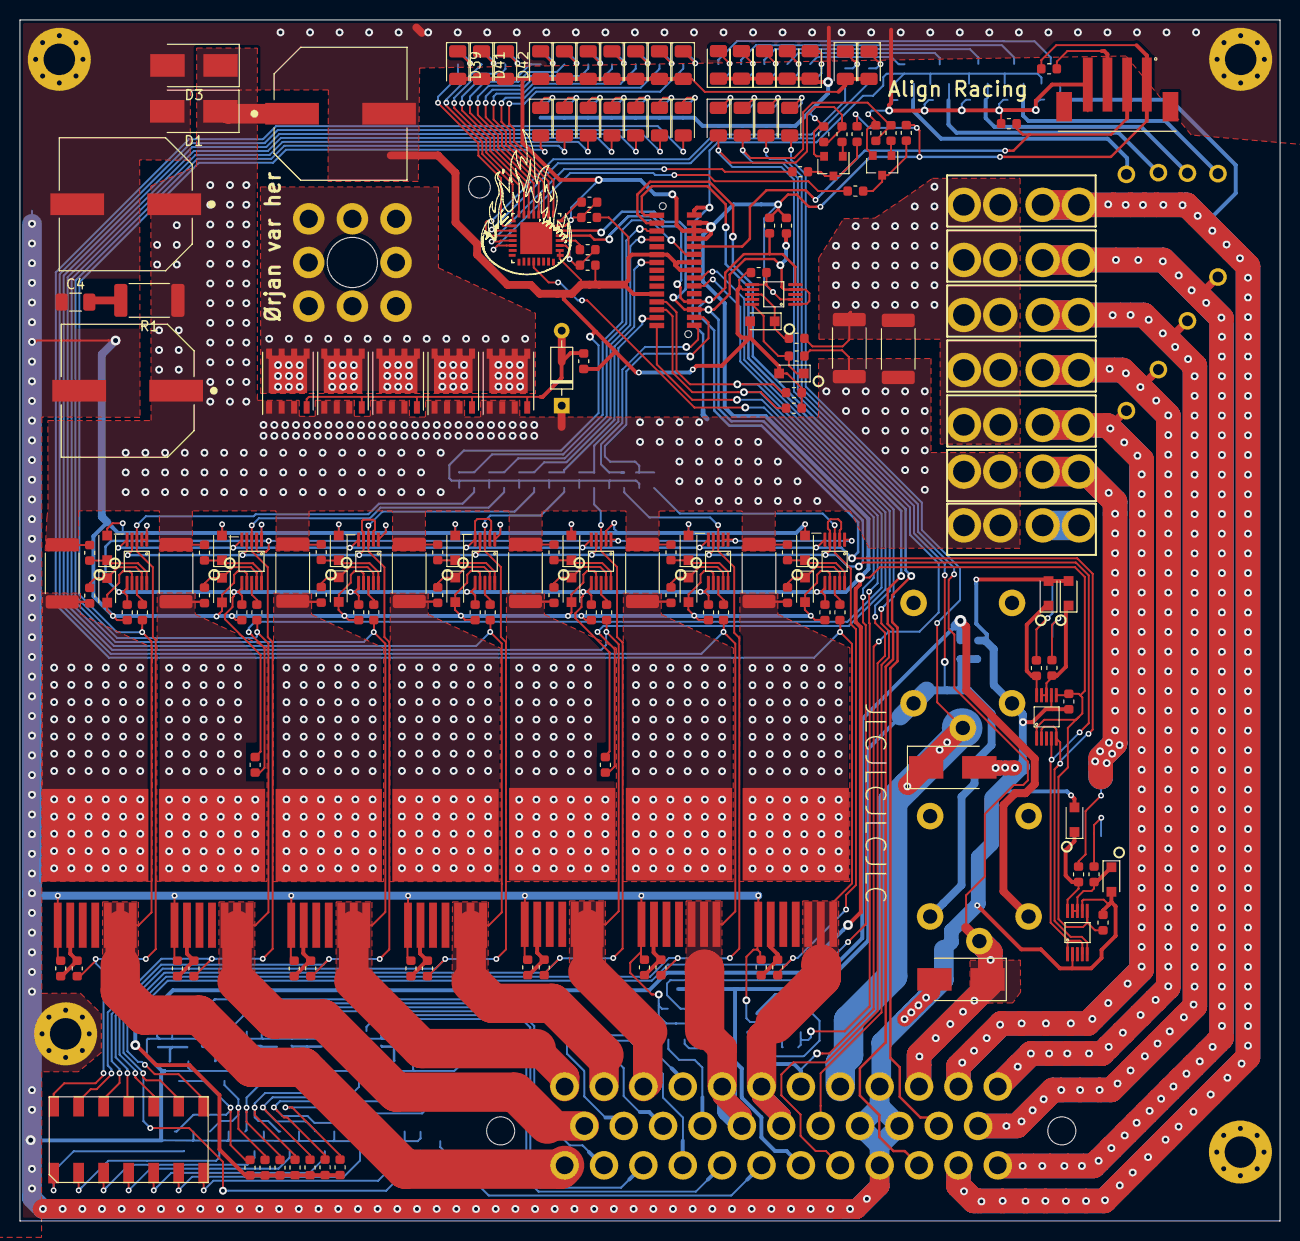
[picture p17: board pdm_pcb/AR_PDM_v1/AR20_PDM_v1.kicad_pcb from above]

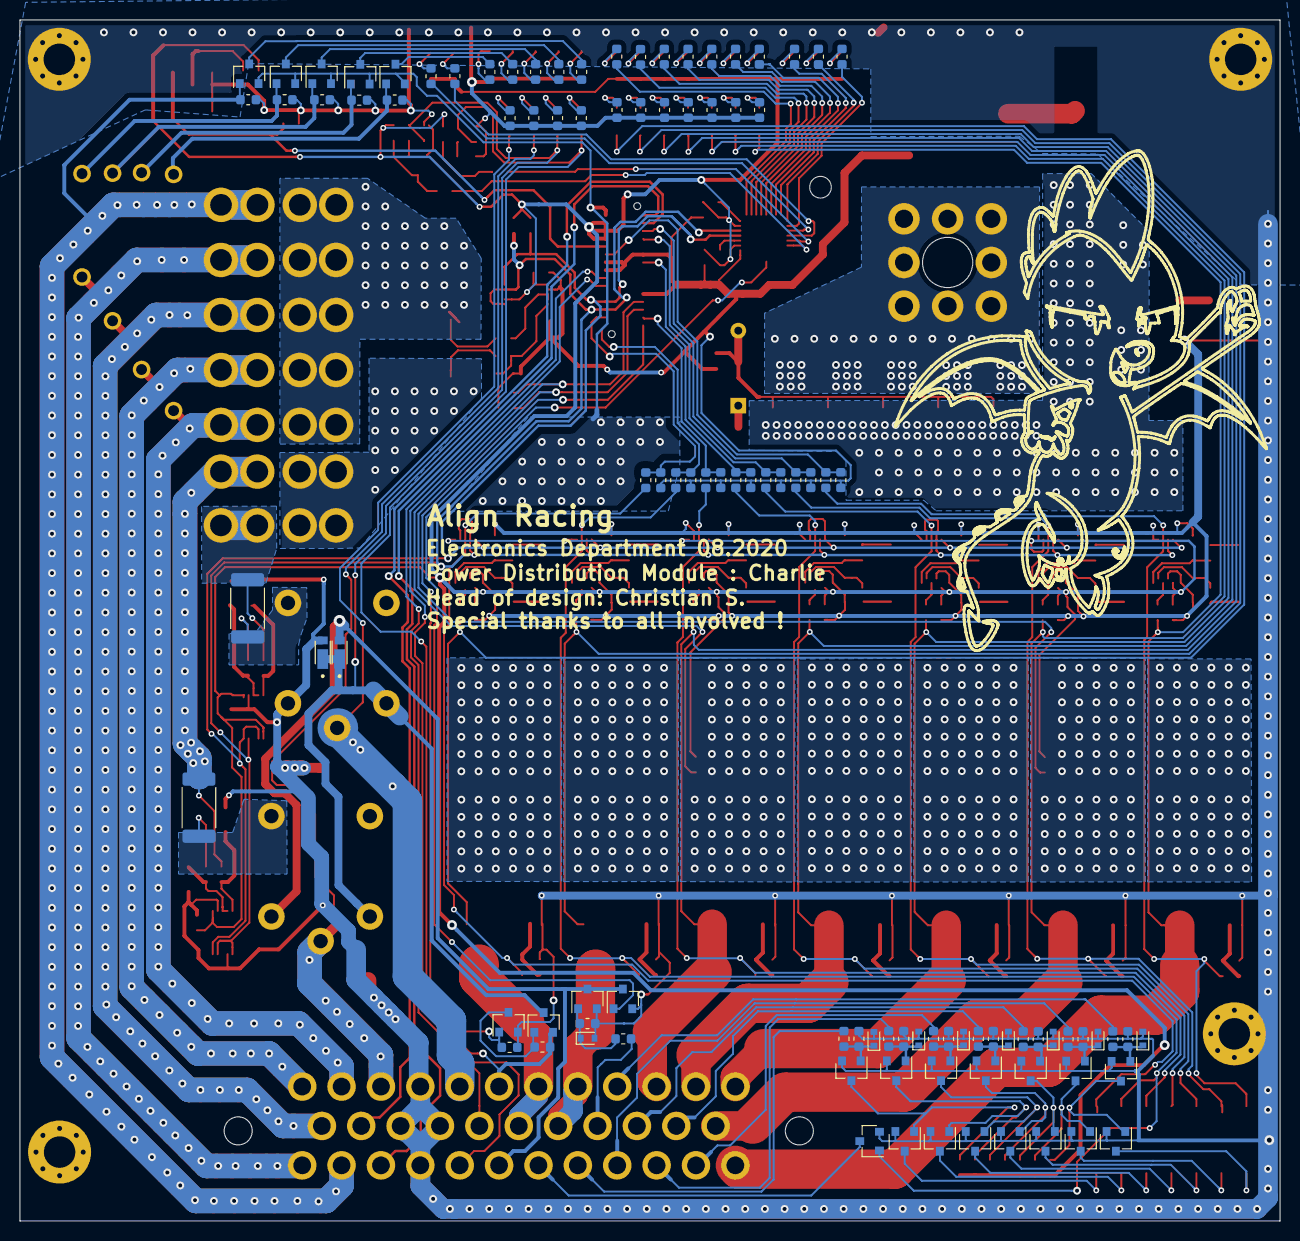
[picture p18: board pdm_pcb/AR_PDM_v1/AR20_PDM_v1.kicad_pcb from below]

Board: 2 copper layers, 128.0 x 122.0 mm, 294 parts (101 on the bottom side), 184 nets.

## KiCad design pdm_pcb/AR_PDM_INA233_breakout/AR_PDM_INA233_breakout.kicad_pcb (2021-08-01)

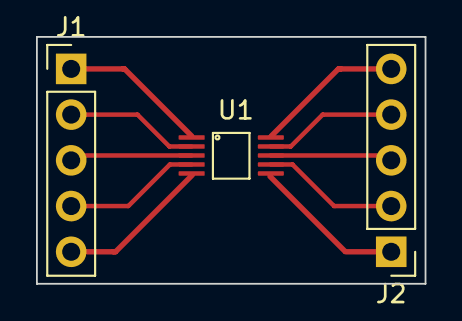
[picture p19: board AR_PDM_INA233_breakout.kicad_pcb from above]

Board: 2 copper layers, 21.6 x 13.7 mm, 3 parts (0 on the bottom side), 10 nets.

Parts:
J1, J2: Conn_01x05_Male; PinHeader_1x05_P2.54mm_Vertical
U1: INA233

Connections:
GND: J2.2, U1.7
IN+: J2.5, U1.10
IN-: J2.4, U1.9
unnamed: J1.1, U1.1
unnamed: J1.2, U1.2
unnamed: J1.3, U1.3
unnamed: J1.4, U1.4
unnamed: J1.5, U1.5
VBUS: J2.3, U1.8
VS: J2.1, U1.6

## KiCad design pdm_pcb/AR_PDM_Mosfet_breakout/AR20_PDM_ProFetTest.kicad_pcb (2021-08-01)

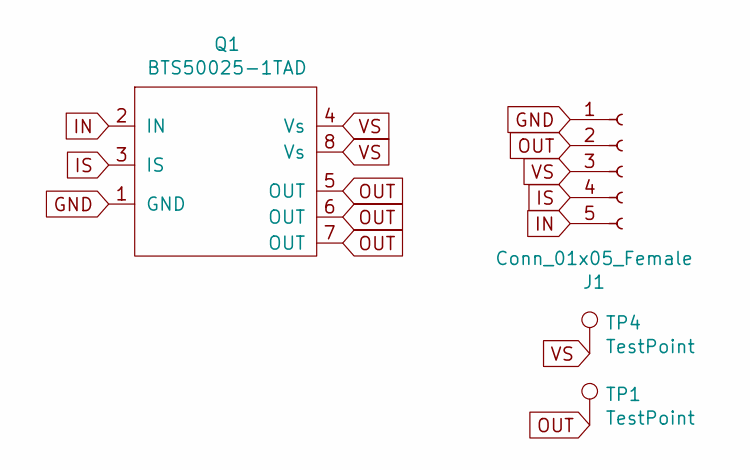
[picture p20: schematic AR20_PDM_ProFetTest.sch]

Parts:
J1: Conn_01x05_Female; PinHeader_1x05_P2.54mm_Vertical
Q1: BTS50025-1TAD; BTS500xx
TP1, TP4: TestPoint; Supp_THT_Hole

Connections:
GND: J1.1, Q1.1 (GND)
IN: J1.5, Q1.2 (IN)
IS: J1.4, Q1.3 (IS)
OUT: J1.2, Q1.5 (OUT), Q1.6 (OUT), Q1.7 (OUT), TP1.1
VS: J1.3, Q1.4 (Vs), Q1.8 (Vs), TP4.1


Board: 2 copper layers, 26.7 x 27.9 mm, 4 parts (0 on the bottom side), 5 nets.

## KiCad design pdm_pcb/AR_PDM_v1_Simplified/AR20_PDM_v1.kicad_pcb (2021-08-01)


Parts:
C4, C5, C6, C7, C8, C9, C10: 150nf; C_0603_1608Metric
D1, D3: D_Schottky_MBRS3200T3G; D_SMB_Handsoldering
F1, F2, F3, F4, F5, F9, F10, F11, F12, F13, F14, F15: Fuse; FuseHolder
H1, H2, H3, H4: MountingHole; MountingHole_3.2mm_M3_Pad_Via
J1: High_Curret_terminal; Wurth_74655095R_Screw_Post
J2: 1-776163-1; TE_1-776163-1
Q2, Q3, Q4, Q5, Q6, Q7, Q8: BTS50025-1TAD; BTS500xx
R2, R106: NTC; R_0603_1608Metric
R4, R6, R8, R9, R10, R11, R12, R13, R14, R15, R16, R17, R18, R19: 4k7; R_0603_1608Metric
R7, R107: 10K; R_0603_1608Metric
U1: ACM_2020; ACM_2020_Footprint_wo_silk
U2: N-MOS; N-MOS-DMN6140L-13

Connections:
ACM_Shutdown_Circuit: U1.1 (14/A0-PC0); also elsewhere on the board
CAN_HIGH: J2.22, U1.27 (CAN-H)
CAN_LOW: J2.33, U1.29 (CAN-L)
COIL_INJECTOR_OUT: J2.8; also elsewhere on the board
F1: F1.1, J2.11; also elsewhere on the board
F2: F2.1, J2.12; also elsewhere on the board
F3: F3.1, J2.23; also elsewhere on the board
F4: F4.1, J2.35; also elsewhere on the board
F5: F5.1, J2.34; also elsewhere on the board
F9_P1: F9.2, Q2.8 (Vs); also elsewhere on the board
F10_P2: F10.2, Q3.8 (Vs); also elsewhere on the board
F11_P3: F11.2, Q4.8 (Vs); also elsewhere on the board
F12_P4: F12.2, Q5.8 (Vs); also elsewhere on the board
F13_P5: F13.2, Q6.8 (Vs); also elsewhere on the board
F14_P6: F14.2, Q7.8 (Vs); also elsewhere on the board
F15_P7: F15.2, Q8.8 (Vs); also elsewhere on the board
FP_ENABLE_ACM: U1.22 (4-PD4); also elsewhere on the board
FP_ENABLE_AUX: J2.16; also elsewhere on the board
FP_ENABLE_RELAY_SINK: J2.30; also elsewhere on the board
FUEL_PUMP_OUT: J2.10; also elsewhere on the board
unnamed: C4.1, Q2.2 (IN), R6.1
unnamed: C5.1, Q3.2 (IN), R9.1
unnamed: C6.1, Q4.2 (IN), R11.1
unnamed: C7.1, Q5.2 (IN), R13.1
unnamed: C8.1, Q6.2 (IN), R15.1
unnamed: C9.1, Q7.2 (IN), R17.1
unnamed: C10.1, Q8.2 (IN), R19.1
unnamed: R2.2, R7.2, U1.7 (ADC6)
unnamed: R106.2, R107.2, U1.5 (ADC7)
P1_EN: R4.1, R6.2, U1.20 (3-PD3); also elsewhere on the board
P1_EN_AUX: J2.4; also elsewhere on the board
P1_OUT: J2.24, Q2.5 (OUT), Q2.6 (OUT), Q2.7 (OUT); also elsewhere on the board
P2_EN: R8.1, R9.2, U1.25 (5-PD5); also elsewhere on the board
P2_EN_AUX: J2.27; also elsewhere on the board
P2_OUT: J2.13, Q3.5 (OUT), Q3.6 (OUT), Q3.7 (OUT); also elsewhere on the board
P3_EN: R10.1, R11.2, U1.23 (6-PD6); also elsewhere on the board
P3_EN_AUX: J2.15; also elsewhere on the board
P3_OUT: J2.1, Q4.5 (OUT), Q4.6 (OUT), Q4.7 (OUT); also elsewhere on the board
P4_EN: R12.1, R13.2, U1.17 (10-PB2-SS); also elsewhere on the board
P4_EN_AUX: J2.14; also elsewhere on the board
P4_OUT: J2.2, Q5.5 (OUT), Q5.6 (OUT), Q5.7 (OUT); also elsewhere on the board
P5_EN: R14.1, R15.2, U1.3 (15/A1-PC1); also elsewhere on the board
P5_EN_AUX: J2.25; also elsewhere on the board
P5_OUT: J2.3, Q6.5 (OUT), Q6.6 (OUT), Q6.7 (OUT); also elsewhere on the board
P6_EN: R16.1, R17.2, U1.2 (16/A2-PC2), U2.1 (G); also elsewhere on the board
P6_EN_AUX: J2.26; also elsewhere on the board
P6_GearA_open_drain_output: J2.29, U2.3 (D)
P6_OUT: J2.5, J2.17, Q7.5 (OUT), Q7.6 (OUT), Q7.7 (OUT); also elsewhere on the board
P7_EN: R18.1, R19.2, U1.4 (17/A3-PC3); also elsewhere on the board
P7_EN_AUX: J2.28; also elsewhere on the board
P7_OUT: J2.6, J2.18, Q8.5 (OUT), Q8.6 (OUT), Q8.7 (OUT); also elsewhere on the board
RX: J2.31, U1.12 (0-PD0)
SHUTDOWN_IN: J2.7; also elsewhere on the board
TX: J2.19, U1.14 (1-PD1-TXD)
V+12V: D1.1 (K), D3.1 (K), F1.2, F2.2, F3.2, F4.2, F5.2, F9.1, F10.1, F11.1, F12.1, F13.1, F14.1, F15.1, J1.1, U1.30 (12V); also elsewhere on the board
vcc_5v: R2.1, R106.1, U1.24 (5V), U1.26 (5V), U1.28 (5V); also elsewhere on the board

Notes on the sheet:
eLoss of power, flyback protection. Place relativly near all of the mosfets. Application note; introduction to PROFET, page 12 To keep negative voltage spike low, a single diode in series is used. Two for redundancy
insert resistor into gate, to prevent stress onto acm.


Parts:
D30, D31: D_Schottky_SS16M RS; Diode-SODFL2512X73N
D40: D_Zener_BZX585-C15,115; Diode-BZX585-C15,115
D48, D50: D_Schottky_MBRS3200T3G; D_SMB_Handsoldering
F6, F7: Fuse; FuseHolder
K1, K2: DIPxx-1Cxx-51x; Relay_wo_silkscreen
R5, R89, R92: 4K7; R_0603_1608Metric
R105: 4k7; R_0603_1608Metric
U11, U13, U14: N-MOS; N-MOS-DMN6140L-13
U12: P-MOS; P-MOS-BSS83PH6327XTSA1

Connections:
ACM_Shutdown_Circuit: R89.2, U11.1 (G); also elsewhere on the board
COIL_INJECTOR_OUT: D48.1 (K), K1.7; also elsewhere on the board
F6_PF_Relay: F6.2, K2.14; also elsewhere on the board
F7_COIL_Relay: F7.2, K1.14; also elsewhere on the board
FP_ENABLE_ACM: U13.1 (G); also elsewhere on the board
FP_ENABLE_AUX: R105.2; also elsewhere on the board
FP_ENABLE_RELAY_SINK: D31.2 (A), K2.2, U13.3 (D), U14.3 (D); also elsewhere on the board
FUEL_PUMP_OUT: D50.1 (K), K2.7; also elsewhere on the board
unnamed: D40.1 (K), R92.1, R105.1, U14.1 (G)
unnamed: R5.1, U11.3 (D), U12.1 (G)
SHUTDOWN_IN: R5.2, U12.2 (S); also elsewhere on the board
Shutdown_Relay_Side: D30.1 (K), D31.1 (K), K1.6, K2.6, U12.3 (D); also elsewhere on the board
V+12V: F6.1, F7.1; also elsewhere on the board

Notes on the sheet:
Use Logic Level Mosfets. (Gs Threshold <3.3V)


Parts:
D23, D24, D26, D27, D28, D29, D32: D_Zener_BZX585-C15,115; Diode-BZX585-C15,115
R38, R39, R40, R41, R42, R43, R44, R46, R48, R49, R50, R52, R54, R56, R57, R58, R60, R62, R63, R65, R66, R69, R70, R72, R73, R74, R75, R78, R79, R80, R81, R82, R83, R84, R85: 4k7; R_0603_1608Metric
U16, U17, U18, U19, U20, U21, U22, U23, U24, U25, U26, U27, U28, U29: N-MOS; N-MOS-DMN6140L-13

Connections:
unnamed: D23.1 (K), R38.1, R42.1, U16.1 (G)
unnamed: D24.1 (K), R39.1, R43.1, U17.1 (G)
unnamed: D26.1 (K), R40.1, R44.1, U18.1 (G)
unnamed: D27.1 (K), R41.1, R46.1, U19.1 (G)
unnamed: D28.1 (K), R66.1, R72.1, U24.1 (G)
unnamed: D29.1 (K), R69.1, R73.1, U25.1 (G)
unnamed: D32.1 (K), R70.1, R74.1, U26.1 (G)
unnamed: R48.1, U16.3 (D), U20.1 (G)
unnamed: R49.1, U17.3 (D), U21.1 (G)
unnamed: R50.1, U18.3 (D), U22.1 (G)
unnamed: R52.1, U19.3 (D), U23.1 (G)
unnamed: R54.1, R60.2, U20.3 (D)
unnamed: R56.1, R62.2, U21.3 (D)
unnamed: R57.1, R63.2, U22.3 (D)
unnamed: R58.1, R65.2, U23.3 (D)
unnamed: R75.1, U24.3 (D), U27.1 (G)
unnamed: R78.1, U25.3 (D), U28.1 (G)
unnamed: R79.1, U26.3 (D), U29.1 (G)
unnamed: R80.1, R83.2, U27.3 (D)
unnamed: R81.1, R84.2, U28.3 (D)
unnamed: R82.1, R85.2, U29.3 (D)
P1_EN: R60.1; also elsewhere on the board
P1_EN_AUX: R38.2; also elsewhere on the board
P2_EN: R62.1; also elsewhere on the board
P2_EN_AUX: R39.2; also elsewhere on the board
P3_EN: R63.1; also elsewhere on the board
P3_EN_AUX: R40.2; also elsewhere on the board
P4_EN: R65.1; also elsewhere on the board
P4_EN_AUX: R41.2; also elsewhere on the board
P5_EN: R83.1; also elsewhere on the board
P5_EN_AUX: R66.2; also elsewhere on the board
P6_EN: R84.1; also elsewhere on the board
P6_EN_AUX: R69.2; also elsewhere on the board
P7_EN: R85.1; also elsewhere on the board
P7_EN_AUX: R70.2; also elsewhere on the board
vcc_5v: R48.2, R49.2, R50.2, R52.2, R54.2, R56.2, R57.2, R58.2, R75.2, R78.2, R79.2, R80.2, R81.2, R82.2; also elsewhere on the board

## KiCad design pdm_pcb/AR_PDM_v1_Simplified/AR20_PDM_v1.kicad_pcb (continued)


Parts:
D2, D4: F1_Fault; LED_1206_3216Metric
D5, D7: F2_Fault; LED_1206_3216Metric
D6: Led_Green_P1_Active; LED_1206_3216Metric
D8: Led_Green_P2_Active; LED_1206_3216Metric
D9, D25: F3_Fault; LED_1206_3216Metric
D10: Led_Green_P3_Active; LED_1206_3216Metric
D11, D35: F4_Fault; LED_1206_3216Metric
D12: Led_Green_P4_Active; LED_1206_3216Metric
D13, D36: F5_Fault; LED_1206_3216Metric
D14: Led_Green_P5_Active; LED_1206_3216Metric
D15, D37: F6_Fault; LED_1206_3216Metric
D16: Led_Green_P6_Active; LED_1206_3216Metric
D17, D38: F7_Fault; LED_1206_3216Metric
D18: Led_Green_P7_Active; LED_1206_3216Metric
D19: Led_Green_FP_Active; LED_1206_3216Metric
D20: Led_Green_COIL_INJ_Active; LED_1206_3216Metric
D21: Led_Green_Shutdown_Circuit_Supply; LED_1206_3216Metric
D22: Led_Green_Shutdown_IN_Active; LED_1206_3216Metric
R20, R21, R24, R25, R28, R30, R32, R34, R36, R76, R96, R98, R100, R102: 4k7; R_0603_1608Metric
R22, R23, R26, R27, R29, R31, R33, R35, R37, R45, R47, R51, R53, R55, R59, R61, R64, R67, R68, R71, R77, R97, R99, R101, R103: 2K; R_0603_1608Metric
U3, U4, U5, U6, U7, U8, U9, U10, U15, U32, U33, U34, U35, U36: P-MOS; P-MOS-BSS83PH6327XTSA1

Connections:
COIL_INJECTOR_OUT: D20.2 (A); also elsewhere on the board
F1: R21.1, U4.1 (G); also elsewhere on the board
F2: R25.1, U6.1 (G); also elsewhere on the board
F3: R28.1, U7.1 (G); also elsewhere on the board
F4: R30.1, U8.1 (G); also elsewhere on the board
F5: R32.1, U9.1 (G); also elsewhere on the board
F6_PF_Relay: R34.1, U10.1 (G); also elsewhere on the board
F7_COIL_Relay: R36.1, U15.1 (G); also elsewhere on the board
F9_P1: R20.1, U3.1 (G); also elsewhere on the board
F10_P2: R24.1, U5.1 (G); also elsewhere on the board
F11_P3: R76.1, U32.1 (G); also elsewhere on the board
F12_P4: R96.1, U33.1 (G); also elsewhere on the board
F13_P5: R98.1, U34.1 (G); also elsewhere on the board
F14_P6: R100.1, U35.1 (G); also elsewhere on the board
F15_P7: R102.1, U36.1 (G); also elsewhere on the board
FUEL_PUMP_OUT: D19.2 (A); also elsewhere on the board
unnamed: D2.2 (A), R22.2
unnamed: D4.2 (A), R23.2
unnamed: D5.2 (A), R26.2
unnamed: D6.1 (K), R45.1
unnamed: D7.2 (A), R27.2
unnamed: D8.1 (K), R47.1
unnamed: D9.2 (A), R29.2
unnamed: D10.1 (K), R51.1
unnamed: D11.2 (A), R31.2
unnamed: D12.1 (K), R53.1
unnamed: D13.2 (A), R33.2
unnamed: D14.1 (K), R55.1
unnamed: D15.2 (A), R35.2
unnamed: D16.1 (K), R59.1
unnamed: D17.2 (A), R37.2
unnamed: D18.1 (K), R61.1
unnamed: D19.1 (K), R64.1
unnamed: D20.1 (K), R67.1
unnamed: D21.1 (K), R68.1
unnamed: D22.1 (K), R71.1
unnamed: D25.2 (A), R77.2
unnamed: D35.2 (A), R97.2
unnamed: D36.2 (A), R99.2
unnamed: D37.2 (A), R101.2
unnamed: D38.2 (A), R103.2
unnamed: R22.1, U3.3 (D)
unnamed: R23.1, U4.3 (D)
unnamed: R26.1, U5.3 (D)
unnamed: R27.1, U6.3 (D)
unnamed: R29.1, U7.3 (D)
unnamed: R31.1, U8.3 (D)
unnamed: R33.1, U9.3 (D)
unnamed: R35.1, U10.3 (D)
unnamed: R37.1, U15.3 (D)
unnamed: R77.1, U32.3 (D)
unnamed: R97.1, U33.3 (D)
unnamed: R99.1, U34.3 (D)
unnamed: R101.1, U35.3 (D)
unnamed: R103.1, U36.3 (D)
P1_OUT: D6.2 (A); also elsewhere on the board
P2_OUT: D8.2 (A); also elsewhere on the board
P3_OUT: D10.2 (A); also elsewhere on the board
P4_OUT: D12.2 (A); also elsewhere on the board
P5_OUT: D14.2 (A); also elsewhere on the board
P6_OUT: D16.2 (A); also elsewhere on the board
P7_OUT: D18.2 (A); also elsewhere on the board
SHUTDOWN_IN: D22.2 (A); also elsewhere on the board
Shutdown_Relay_Side: D21.2 (A); also elsewhere on the board
V+12V: U3.2 (S), U4.2 (S), U5.2 (S), U6.2 (S), U7.2 (S), U8.2 (S), U9.2 (S), U10.2 (S), U15.2 (S), U32.2 (S), U33.2 (S), U34.2 (S), U35.2 (S), U36.2 (S); also elsewhere on the board

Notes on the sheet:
Activity LED for mechanical/relay power. GREEN LEDS

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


Board: 4 copper layers, 128.0 x 122.0 mm, 205 parts (108 on the bottom side), 122 nets.

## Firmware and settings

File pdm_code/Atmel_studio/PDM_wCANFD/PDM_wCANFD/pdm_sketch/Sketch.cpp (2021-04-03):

// ___________ 3RD PARTY LIBRARIES _____________ //
//#include "MemoryFree.h"

// ___________ PDM/ALIGN LIBRARIES _____________ //
#include "INA233.h"
#include "Port_expander.h"
#include "Config.h"
#include "errorHandler.h"

// ___________ ARDUINO LIBRARIES ______________ //
#include <Arduino.h>
//#include <SPI.h>
#include <avr/wdt.h>
#include "Wire.h"
#include <ACAN2517FD.h>
#include <SPI.h>



// ___________________________ CANBUS SETTINGS ______________________________//
static const byte MCP2517_CS  = 7 ; // CS input of MCP2517
static const byte MCP2517_INT =  2 ; // INT output of MCP2517

ACAN2517FD can (MCP2517_CS, SPI, MCP2517_INT);
	CANFDMessage frame_FD, frame;



// ___________________________ INA233 AND MOSFET/RLE SETUP ______________________________//
class  mosfet{
public:
	mosfet() = delete;
	mosfet(uint8_t MOSpin) : MOSpin_(MOSpin){
		pinMode(MOSpin_, OUTPUT);
	}
	
	// Complete circuit
	void close_MOSFET(){
		digitalWrite(MOSpin_, HIGH);
	}
	
	// Break circuit
	void open_MOSFET(){
		digitalWrite(MOSpin_, LOW);
	}
private:	
	uint8_t MOSpin_;
};

union cantypes{
	uint8_t u8[4];
	int16_t u16[2];
	float f;
	};

cantypes CT_1, CT_2;

// Functions and global variables
void check_INA233_miscommunication();
ErrorHandler errorHandler();
uint16_t default_address = 0b0100011100100111;
unsigned long timeStamps[10] = {0};


// creating each INA233 sensor object
INA233_S Sensor_1(adrSensor1, m_valueSensor1, cal_valueSensor1, alarmConfigSensor1), 
		Sensor_2(adrSensor2, m_valueSensor2, cal_valueSensor2, alarmConfigSensor2),
		Sensor_3(adrSensor2, m_valueSensor2, cal_valueSensor2, alarmConfigSensor2),
		Sensor_4(adrSensor2, m_valueSensor2, cal_valueSensor2, alarmConfigSensor2),
		Sensor_5(adrSensor2, m_valueSensor2, cal_valueSensor2, alarmConfigSensor2),
		Sensor_6(adrSensor2, m_valueSensor2, cal_valueSensor2, alarmConfigSensor2),
		Sensor_7(adrSensor2, m_valueSensor2, cal_valueSensor2, alarmConfigSensor2);


// Adding each sensor to an array of pointers for easier use in loops and repeated actions
// INA233 [0 to 6] are the mosfets, [7 to 9] others
INA233_S* SensorList[] = { &Sensor_1, &Sensor_2, &Sensor_3, &Sensor_4, &Sensor_5, &Sensor_6, &Sensor_7 };


// Create instances of each mosfet object
mosfet	p1(p1_ACM_E_Pin), 
		p2(p2_ACM_E_Pin), 
		p3(p3_ACM_E_Pin), 
		p4(p4_ACM_E_Pin),
		p5(p5_ACM_E_Pin),
		p6(p6_ACM_E_Pin),
		p7(p7_ACM_E_Pin);

// Adding each mosfet object to a pointer array for easier loops
mosfet* MosfetList[] = { &p1, &p2, &p3, &p4, &p5, &p6, &p7 };
	
//TI_TCA6424A_S expander (adrExpander);



void blink_light();
uint8_t STATE = HIGH, STATE2 = HIGH;
unsigned long blink_time = 0, blink_interval = 500;

void setup() {	
	wdt_enable(WDTO_500MS);
	
	Wire.begin();
	Wire.setClock(10000);
	//Serial.begin(9600);
	
	pinMode(9, OUTPUT);
	
	// Setup for each INA233 sensor
	for (uint8_t ii = 0; ii < 7; ii++){
		SensorList[ii]->initialize();
	}

	for (uint8_t ii = 0; ii < 7; ii++){
		SensorList[ii]->setADC_Settings(default_address);
	}
	
	
	// ___________________________ START SPI ______________________________//
	SPI.begin () ;
		// For version >= 2.1.0
	ACAN2517FDSettings settings (ACAN2517FDSettings::OSC_20MHz, 500UL * 1000UL, DataBitRateFactor::x8);
		/* For version < 2.1.0
			ACAN2517FDSettings settings (ACAN2517FDSettings::OSC_20MHz, 125UL * 1000UL, ACAN2517FDSettings::DATA_BITRATE_x8);*/
	settings.mRequestedMode = ACAN2517FDSettings::NormalFD;
	
	// Default values are too high for an Arduino Uno that contains 2048 bytes of RAM: reduce them
	settings.mDriverTransmitFIFOSize = 1;
	settings.mDriverReceiveFIFOSize = 1;
	
	
	// ___________________________ RAM USAGE ______________________________//
	Serial.print ("MCP2517FD RAM Usage: ");
	Serial.print (settings.ramUsage());
	Serial.println (" bytes");
	
	
	// ___________________________ CAN BEGIN ______________________________//
	const uint32_t errorCode = can.begin (settings, [] { can.isr(); });
	if (errorCode != 0) {
		Serial.print ("Configuration error 0x");
		Serial.println (errorCode, HEX);
	}
	
	for (int ii = 0; ii < 64; ii++){
		frame_FD.data[ii] = ii;
	}
	for (int ii = 0; ii < 8; ii++){
		frame.data[ii] = ii;
	}
	frame.len = 8;
	frame_FD.len = 64; // Valid lengths are: 0, 1, ..., 8, 12, 16, 20, 24, 32, 48, 64
	frame.type = CANFDMessage::CAN_DATA;
	frame_FD.type = CANFDMessage::CANFD_WITH_BIT_RATE_SWITCH;
	
	frame.id = 0x500;
	frame_FD.id = 0x501;
	
	
	
	// Let power through mosfets
	for (uint8_t ii = 0; ii < 7; ii++){
		MosfetList[ii]->close_MOSFET();
	}
}


void loop() {
	
	// Make sure communication with INA233 still works, if not then open mosfet
	check_INA233_miscommunication();
	
	float current_1 = Sensor_1.getCurrent();
	int test = 1;
	
	Serial.println(current_1);
	
	if (can.available ()) {
		can.receive (frame_FD);
		Serial.print ("Received: ");
		
		if (frame_FD.data[0] == 0x01){
			digitalWrite(9, HIGH);
			MosfetList[1]->close_MOSFET();
		}

		if (frame_FD.data[0] == 0x02){
			digitalWrite(9, LOW);
			MosfetList[1]->open_MOSFET();
		}		
	}
	if (millis() - timeStamps[1] > 100){		
		frame.id = 0x10;
		frame.len = 4;
		float temp_test = 1.34;
		float temp_current = Sensor_2.getCurrent() * 100;
		float temp_voltage_L = Sensor_2.getVoltage_L() * 10;
		int16_t current_int = (int16_t)(temp_current);
		int16_t voltage_int = (int16_t)(temp_voltage_L);
		
		CT_1.u16[0] = current_int;
		CT_1.u16[1] = voltage_int;
		
		frame.data[0] = CT_1.u8[0];
		frame.data[1] = CT_1.u8[1];
		frame.data[2] = CT_1.u8[2];
		frame.data[3] = CT_1.u8[3];
				
		
		can.tryToSend(frame);
		
		
		timeStamps[1] = millis();
	}
	//blink_light();
	
	wdt_reset();	
}

void check_INA233_miscommunication(){
	
	if((millis() - timeStamps[0]) > interval_INA233_checking){
		
		for (uint8_t ii = 0; ii < 7; ii++){
			// If communication is not responding properly, open mosfet
			if(SensorList[ii]->testCommunication() == 1){
				MosfetList[ii]->open_MOSFET();
			}
		}		
		timeStamps[0] = millis();
	}
}

void blink_light(){
	if (millis() - blink_time > blink_interval){
		STATE = !STATE;
		digitalWrite(9, STATE);
		
		blink_time = millis();
	}
}

/*
void fanControl(){
	
	if(millis() - timeStamps[1] > interval_fanControl){
		
		
		timeStamps[1] = millis();
	}
}


void gear(){

	if(millis() - timeStamps[3] > interval_gear){
		
		
		timeStamps[3] = millis();
	}

}

	
void sendDataOverCan(){
	
	if(millis() - timeStamps[4] > interval_sendDataOverCAN){
		
		
		timeStamps[4] = millis();
	}	
	
}
	
void readDataOverCAN(){
	
	if(millis() - timeStamps[4] > interval_readDataOverCAN){
		
		
		timeStamps[4] = millis();
	}	
	
}
*/

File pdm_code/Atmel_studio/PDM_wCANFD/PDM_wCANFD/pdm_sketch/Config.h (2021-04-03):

#ifndef Config
#define Config
#include "arduino.h"
#include "INA233.h"


const uint16_t interval_INA233_checking = 100;
const uint16_t interval_fanControl = 10000;
const uint16_t interval_gear = 10000;
const uint16_t interval_sendDataOverCAN = 10000;
const uint16_t interval_readDataOverCAN = 10000;

//////Configuration: Protection limits, whole amperes and volts. 0 = OFF \\\\\\//////  
const float ov_Sensor1 = 13;    //Over voltage output 1
const float uv_Sensor1 = 0;     //Under voltage output 1
const float oc_Sensor1 = 2;     //Over Current output 1

const float ov_Sensor2 = 13;    //Over voltage output 2
const float uv_Sensor2 = 0;     //Under voltage output 2
const float oc_Sensor2 = 2;     //Over Current output 2

const float ov_Sensor3 = 13;    //Over voltage output 3
const float uv_Sensor3 = 0;     //Under voltage output 3
const float oc_Sensor3 = 2;     //Over Current output 3

const float ov_Sensor4 = 13;    //Over voltage output 4
const float uv_Sensor4 = 0;     //Under voltage output 4
const float oc_Sensor4 = 2;     //Over Current output 4

const float ov_Sensor5 = 13;    //Over voltage output 5
const float uv_Sensor5 = 0;     //Under voltage output 5
const float oc_Sensor5 = 2;     //Over Current output 5

const float ov_Sensor6 = 13;    //Over voltage output 6
const float uv_Sensor6 = 0;     //Under voltage output 6
const float oc_Sensor6 = 2;     //Over Current output 6

const float ov_Sensor7 = 13;    //Over voltage output 7
const float uv_Sensor7 = 0;     //Under voltage output 7
const float oc_Sensor7 = 2;     //Over Current output 7

//////END Configuration \\\\\\//////  

//FROM HERE ON - DO NOT TOUCH \\//FROM HERE ON - DO NOT TOUCH \\////FROM HERE ON - DO NOT TOUCH \\//

const INA233_Alarm_Config alarmConfigSensor1{oc_Sensor1, ov_Sensor1, uv_Sensor1};
const INA233_Alarm_Config alarmConfigSensor2{oc_Sensor2, ov_Sensor2, uv_Sensor2};
const INA233_Alarm_Config alarmConfigSensor3{oc_Sensor3, ov_Sensor3, uv_Sensor3};
const INA233_Alarm_Config alarmConfigSensor4{oc_Sensor4, ov_Sensor4, uv_Sensor4};
const INA233_Alarm_Config alarmConfigSensor5{oc_Sensor5, ov_Sensor5, uv_Sensor5};
const INA233_Alarm_Config alarmConfigSensor6{oc_Sensor6, ov_Sensor6, uv_Sensor6};
const INA233_Alarm_Config alarmConfigSensor7{oc_Sensor7, ov_Sensor7, uv_Sensor7};

// Addresses for MOSFET INA233
const uint8_t adrSensor1 = 0x40;
const uint8_t adrSensor2 = 0x41;
const uint8_t adrSensor3 = 0x42;
const uint8_t adrSensor4 = 0x43;
const uint8_t adrSensor5 = 0x44;
const uint8_t adrSensor6 = 0x45;
const uint8_t adrSensor7 = 0x46;

const uint8_t adrExpander = 0x22;

const uint16_t m_valueSensor1 = 820;
const uint16_t m_valueSensor2 = 820;
const uint16_t m_valueSensor3 = 820;
const uint16_t m_valueSensor4 = 820;
const uint16_t m_valueSensor5 = 820;
const uint16_t m_valueSensor6 = 820;
const uint16_t m_valueSensor7 = 820;

const uint16_t cal_valueSensor1 = 2099; 
const uint16_t cal_valueSensor2 = 2099; 
const uint16_t cal_valueSensor3 = 2099; 
const uint16_t cal_valueSensor4 = 2099; 
const uint16_t cal_valueSensor5 = 2099; 
const uint16_t cal_valueSensor6 = 2099; 
const uint16_t cal_valueSensor7 = 2099; 


// Gamle verdier som ikke stemmer med schematics (gamle verdier?)
const uint8_t p1_ACM_E_Pin = 3;
const uint8_t p2_ACM_E_Pin = 5;
const uint8_t p3_ACM_E_Pin = 6;
const uint8_t p4_ACM_E_Pin = 10;
const uint8_t p5_ACM_E_Pin = 15;
const uint8_t p6_ACM_E_Pin = 16;
const uint8_t p7_ACM_E_Pin = 17;
const uint8_t shutdown_ACM_Pin = 14;

#endif

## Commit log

2019-06-10 Added: AR19-ACM
    [ACM_Y2019V0.1.sch]
2019-07-24 First design of ACM2020
    [ACM_Y2020V0.1.kicad_pcb, ACM_Y2020V0.1.sch]
2019-07-24 First design of ACM2020 - 2
    [ACM_Y2020V0.1.kicad_pcb]
2019-07-25 Added MCP25625 and PDFS
    [ACM_Y2020V0.1.kicad_pcb, ACM_Y2020V0.1.sch]
2019-07-26 See change log for update.
    [ACM_Y2020V0.1.kicad_pcb, ACM_Y2020V0.1.sch]
2019-07-27 Changelog for 27.07.2019
    [ACM_Y2020V0.1.kicad_pcb, ACM_Y2020V0.1.sch]
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2019-10-20 First sketch of the pdm
    Rough sketch of first e-fuse switch, phase1
    [AR20_PDM_v1.kicad_pcb, AR20_PDM_v1.sch, Phase1.sch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]
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2019-10-30 Refining pdm phase 1
    [AR20_PDM_v1.sch, Phase1.sch]
2019-10-30 Added voltage divider KiCAd
    [Teensy4_header_breakout.kicad_pcb, Teensy4_header_breakout.sch, VoltageDivider.kicad_pcb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]
2019-10-30 PDM Phase 1 mostly complete
    [AR20_PDM_v1.sch, Phase1.sch]
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2019-11-06 Brakelight Shematic 95% ready.
    [AR20_Brakelight.sch]
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2019-11-07 Brakelight PCB 50% ready
    [AR20_Brakelight.kicad_pcb]
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2019-11-13 PDM: VOL1 + Breakout board
    [AR20_PDM_ProFetTest.kicad_pcb, Phase1.sch]
2019-11-18 Separated chematics, and brakout board into two separate folders
    [AR20_PDM_ProFetTest.kicad_pcb, AR20_PDM_v1.kicad_pcb, AR20_PDM_v1.sch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]
2019-11-18 Moved footprints, and libraries in separate folders.
    [AR20_PDM_ProFetTest.sch]
2019-11-18 Revert "Moved footprints, and libraries in separate folders."
    This reverts commit ce8c3de0d6cd9b7318d398a4fba87650c9fee54b.
    [AR20_PDM_ProFetTest.sch]
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2019-11-18 PDM breakout boards and gerber files
    [AR20_PDM_ProFetTest.sch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]
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2019-11-24 First draft of Gear phase, shutdown relays, and Direct phases.
    [AR20_PDM_v1.sch, Fuel_Ignition_Shutdown.sch, Fuses_Direct.sch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]
2019-11-24 Added label on mosfets, added fuel pump sinking output
    [AR20_PDM_v1.sch, Fuel_Ignition_Shutdown.sch, Gear_A.sch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]
2019-11-28 Major update to testcode
    - Set up for visual studio code
    - Re organized structure
    - created INA233 objects
    - Made object oriented structure
    [Phase1.sch]
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2020-01-08 Major Schematics changes-work in progress
    - Added rest of the phases
    - Corrected pin names, and began to connect everything
    - Began mapping the connectors, Pin-out not yet verified for all connectors
    - Began mapping of user interface (Led indicators)
    - INA233 now senses OUT voltage on mosfets instead of main 12Volt
    - Added extra decoupling capacitors
    Known things to fix:
    - AUX inputs activation method, and a disconnect switch on phase 1-7 (mosfets)
    - Rest of the user interface
    - Find correct plugs for the system
    [AR20_PDM_v1.sch, Fuel_Ignition_Shutdown.sch, Fuses_Direct.sch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]
2020-01-10 Added LEDs and switches.
    - Added all status leds
    - Added all switches
    - ! Connections are work in progress, not everything is correct
    [AR20_PDM_v1.sch, Fuses_Direct.sch, Misc.sch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]
2020-01-11 Fixed wrong value components and ports, wiring, see discription
    - Fixed supply cappacitor value 220 nf to 100nf
    - Fixed IN cappacitor value 220 nf to 150 nf
    - Fixed out cappacitor value, 220nf to 10 nf
    - Made a mux for mosfet sense
    - Found a I/O port expander
    - Added some and removed some leds
    - Fixed all labels, and wired everything up, besides the connectors
    - Still missing connector and acm connector pinout.
    [AR20_PDM_v1.sch, Fuel_Ignition_Shutdown.sch, Fuses_Direct.sch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]
2020-01-13 Fixed issues, controlled components, BOM, see discription
    - added acm symbol
    - fixed wrongly faced P-mosfets
    - I/O expander now sinks led instead of source
    - Bill of material mostly done
    - Correct address for INA233 chips.
    - Now 4 diodes serves as flyback for all mosfets
    - Corrected naming scheme for compmonents (everything is not fixed yet)
    - Fixed some labels
    - altso some minor changes
    [AR20_PDM_v1.sch, Fuel_Ignition_Shutdown.sch, Fuses_Direct.sch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]
2020-01-19 PCB design, and issue fixing, work in progress
    - Error fixed: Mux mosfet resistor change to ground
    - Open drain output added on phase 6, for engine blipping purpose
    - Most of pcb symbols and footprints are finished, including main connector
    - PCB is change from 1oz to 2oz copper layer, for easier routing.
    - Basic Draft of pcb is done, for now.
    [AR20_PDM_v1.sch, AR20_PDM_v1_Back.kicad_pcb, Fuel_Ignition_Shutdown.sch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]
2020-01-19 PCB design, and misc, see description, work in progress
    - added shutdown circuit for ACM shutdown capability
    PCB layout, in progress:
    - added copper pour for 12 volt, for fuses
    - arranged indicator LED's
    - arranged some of the P1-P7 caps and resistors
    - re arranged P1-p7 in ascending order.
    [AR20_PDM_v1.kicad_pcb, AR20_PDM_v1.sch, Fuel_Ignition_Shutdown.sch]
2020-01-20 PCB Design, Work in progress
    [AR20_PDM_v1.kicad_pcb, AR20_PDM_v1.sch, Fuel_Ignition_Shutdown.sch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]
2020-01-20 PCB Design, minor schematics changes, work in progress, see description
    - Removed mos sense caps and resistors accept one,
    since only one measurement can be done, at a time.
    - added mos sens protection resistors on each line, to protect mux mosfets and micro controller.
    - Routing plan mostly finalized, some of the traces are just proof of concept.
    those needs to be routed nicely.
    [AR20_PDM_v1.kicad_pcb, AR20_PDM_v1.sch, MOS_SENSE_MUX.sch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]
2020-01-22 First Complete Draft of PCB and schematics, - minus see discription
    - missing correct smd switch header
    - missing correct main power plug
    - tweeks still needs to be done
    - Extra inspection of schematics pending
    - proper, in depth quiality controll of pcb work pending
    [AR20_PDM_v1.kicad_pcb, AR20_PDM_v1.sch, Fuses_Direct.sch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]
2020-01-23 DRC, work Fixed couple of unconnected items
    - Main power connection is still missing
    - Button connector still missing
    [AR20_PDM_v1.kicad_pcb]
2020-01-26 Finilizing the desing, some few missing components
    - Increased the size to accommodate mounting holes
    - Fixed wrong p mos pin out, due to wrong schematics drawing
    - Done alot of tweeeks
    - Button connector still missing.
    [AR20_PDM_v1.kicad_pcb, AR20_PDM_v1.sch, AR20_PDM_v1.step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]
2020-01-28 Alpha version DONE! - Gerber files generated
    - Tweeked
    - checked and re cheked
    - added all missing components
    - Created a really nice silkscreen
    - Ready To Test
    [AR20_PDM_v1-B_Cu.gbr, AR20_PDM_v1-B_Paste.gbr, AR20_PDM_v1-B_SilkS.gbr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]
2020-01-29 Fixed wrong resistors, mos sense. Gerber files updated
    - removed all R_is_protection resistors on each mosfet line
    - added one R_is_protection resistors to mos_sense_all
    ps, mux N-fets, does not need overvoltage protection. 60 volt tolerant.
    [AR20_PDM_v1-B_Cu.gbr, AR20_PDM_v1-B_Paste.gbr, AR20_PDM_v1-B_SilkS.gbr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]
2020-01-29 Calculated and changes i2c pullup Resistors to 2 K
    [AR20_PDM_v1.sch]
2020-01-30 Small tweaks, complete 3d render in ki-cad
    - change switch pin with phase 1 enable, on the mcu, to get phase 1 PWM
    switch can now be sampled with change interrupt.
    - couple of traces beautified
    [ACM-connector-pcb.step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]
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2020-01-30 Solidworks 3d model, almost complete.
    - missing decal, on the back side
    [AR20_PDM_v1.SLDASM, AR20_PDM_v1.kicad_pcb]
2020-02-01 Generated new gerberfile, with forgotten solder mask
    [AR20_PDM_v1-B_Cu.gbl, AR20_PDM_v1-B_Mask.gbs, AR20_PDM_v1-B_Paste.gbp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]
2020-02-26 PDM Testing on the real PCB, Critical bugs found
    working on PDM Improvmente and bugs list,
2020-03-05 This marks end of Alpha version and Beginning of BETA.
    - All relevant test of PDM completed,
    - Improvement and error list generated.
    [Config.h, INA233.cpp, Port_expander.cpp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]
2020-03-06 Major redesign. schematics completed, PCB work in progress
    -TODO : A proper changelog file. Where all changes will apear
    - Redesigned schematics to accommodate errors in the improvement list
    - More detail in ALPHA improvement list
    [AR20_PDM_v1.kicad_pcb, AR20_PDM_v1.sch, Fuel_Ignition_Shutdown.sch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]
2020-03-07 All components in place - PCB work in progress
    [AR20_PDM_v1.kicad_pcb, AR20_PDM_v1.sch, Fuel_Ignition_Shutdown.sch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]
2020-03-08 Pdm version B Draft finished
    [AR20_PDM_v1.kicad_pcb, Main-Mosfet_Switching.sch]
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2020-03-09 Gerber files generated, fixed diode footprint, added misc silkscreen
    [AR20_PDM_v1-B_Cu.gbl, AR20_PDM_v1-B_Mask.gbs, AR20_PDM_v1-B_Paste.gbp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]
2020-03-10 End of Beta beginning of Charlie.
    - RE0.2mm rework, jlc pcb minimum clearance with 2 OZ copper, was not advertised, properly
    a retrace
    Re positioning of some of components
    added temp sensor
    [AR20_PDM_v1.kicad_pcb, AR20_PDM_v1.sch, Fuel_Ignition_Shutdown.sch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]
2020-04-19 Further testing, reveals pdm needs rework
    - As of now, there are major errors in schematics.
    - Needs rework. Version charlie postponed.
    - Very nice pcb layout thats almost finished.
    worth noting this layout for the future
    [AR20_PDM_v1.kicad_pcb, AR20_PDM_v1.sch, Fuel_Ignition_Shutdown.sch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]
2020-06-17 Further testing, reveals pdm needs rework, also really nice layout.
    worth a note for the future
    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
    [AR20_PDM_v1.kicad_pcb, AR20_PDM_v1.sch, Fuel_Ignition_Shutdown.sch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]
2020-06-17 schematics rework
    Fixed INA233 frying due to inductive flyback:
    - Paced ina233 high side of the mosftets
    - New input protection reseistors, and zener diodes, on each ina233.
    Simplified:
    - Removed the MUX and mos sense lines, as i realize that most of this functionality can be obtained trough INA233.
    - Removed some of the cappacitors , besides the most needed ones.
    - removed back to back zener diode configuration, now a single diode insted.
    to reduce negative voltage in case of loss of VS, to be easy on the INA233 filters.
    new stuff:
    - Another temp sensor.
    [AR20_PDM_v1.sch, Fuel_Ignition_Shutdown.sch, Fuses_Direct.sch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]
2020-06-22 Working on pcb layout
    [AR20_PDM_v1.kicad_pcb, AR20_PDM_v1.sch, Fuel_Ignition_Shutdown.sch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]
2020-08-06 PDM mostly complete
    - Reverse polarity protection implemented
    - All traces layed out
    - final polish missing
    - DRC missing
    - Final check missing
    [AR20_PDM_v1.kicad_pcb, AR20_PDM_v1.sch, Fuel_Ignition_Shutdown.sch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]
2020-08-07 Drc work
    Wrong footprint, all else in DRC is good.
    [AR20_PDM_v1.kicad_pcb]
2020-08-08 Fixed a GND trace bug, where trace s accidentaly set to 0.2, DRC work
    [AR20_PDM_v1.kicad_pcb]
2020-08-10 Mostly finalized
    - Fixed alot of the masking
    - Replaced main Flyback diodes to shotky type with low VF
    - Fix DRC one footprint still to small clearance
    - Fix silkscreen
    [AR20_PDM_v1.kicad_pcb, AR20_PDM_v1.sch, Fuel_Ignition_Shutdown.sch]
2020-08-11 All done except port expander footprint
    [AR20_PDM_v1.kicad_pcb]
2020-08-12 PDM V 3 Charlie Finished, awaiting final inspection
    [AR20_PDM_v1.kicad_pcb]
2020-08-22 Gerber files generated, directory cleaned
    [AR20_PDM_v1-B_Cu.gbl, AR20_PDM_v1-B_Mask.gbs, AR20_PDM_v1-B_Paste.gbp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]
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2020-08-22 Re made gerber files
    [AR20_PDM_v1-B_Cu.gbr, AR20_PDM_v1-B_Mask.gbr, AR20_PDM_v1-B_Paste.gbr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]
2020-08-22 Re made gerber files, beware gerber options reset each time
    [AR20_PDM_v1-B_Cu.gbr, AR20_PDM_v1-B_Mask.gbr, AR20_PDM_v1-B_Paste.gbr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]
2020-08-22 Added shutdown circuit monitoring, new gerber files
    [AR20_PDM_v1-B_Cu.gbr, AR20_PDM_v1-B_Mask.gbr, AR20_PDM_v1-B_SilkS.gbr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]
2020-08-22 A litte fix in the shutdown monitoring, new gerber files
    [AR20_PDM_v1-B_Cu.gbr, AR20_PDM_v1-B_Mask.gbr, AR20_PDM_v1-B_SilkS.gbr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]
2020-08-23 shematics adjustments, and fixing values and names
    [AR20_PDM_v1.kicad_pcb, AR20_PDM_v1.sch, Fuel_Ignition_Shutdown.sch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]
2020-08-24 Gerber generated wrongly, Regenerated gerber files
    [AR20_PDM_v1-B_Cu.gbr, AR20_PDM_v1-B_Mask.gbr, AR20_PDM_v1-B_SilkS.gbr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]
2020-09-13 Cleanup Deleted everything than PDM in PDM Branch
    [0ZCM0010FF2G.stp, 17762671.psm, ACM_Box_Standard.SLDPRT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]
2021-01-03 Changer Led Resistor Values
    [User_interface.sch]
2021-02-06 Fixed several errors, updated implementation
    Fixed several syntax errors, made implementation of INA233 1-7 better, properly implemented objects for the mosfets. Also updated Arduinocore folder to not have build errors
    [Config.h, INA233.cpp, INA233.h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]
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2021-03-10 Made new atmel project with CAN included, USE PDM_wCAN
    Created new project to avoid include issues, also more appropriately named foldres/files. Old project still included but it currently has build issues due to the CAN library. Use PDM_wCAN from now on
    [CANFDMessage.h]
2021-03-20 Blinkling LED working
    Blue LED connected to mosfet P4, P1-P7 doesn't work with load connected
    [Sketch.cpp]
2021-04-03 Functional with CAN
    Turning off mosfets with CAN works, INA233 sends back correct values over CAN, fixed minor issue with testcommunication using wrong command
    [Config.h, INA233.cpp, INA233.h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]
2021-05-16 Smiplified PDM design, but still "Snasen"
    Performs all the required duties of a PDM, in a simple and reliable manner. Without the complicated and "Fancy" stuff.
    - Regular automotive blade fuses
    - No digital monitoring
    - Analog user interface
    - No buttons or dip switches.
    - Aux is still present, works in conjunction with ACM.
    [ACM-connector-pcb.step, AR20_PDM_v1-F_Cu.dxf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]
2021-08-01 Directory refactoring and README.md adjustment.
    [ACM-connector-pcb.step, AR20_PDM_ProFetTest.kicad_pcb, AR20_PDM_ProFetTest.sch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]
